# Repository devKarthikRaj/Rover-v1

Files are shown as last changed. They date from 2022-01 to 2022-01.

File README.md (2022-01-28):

# Rover-v1
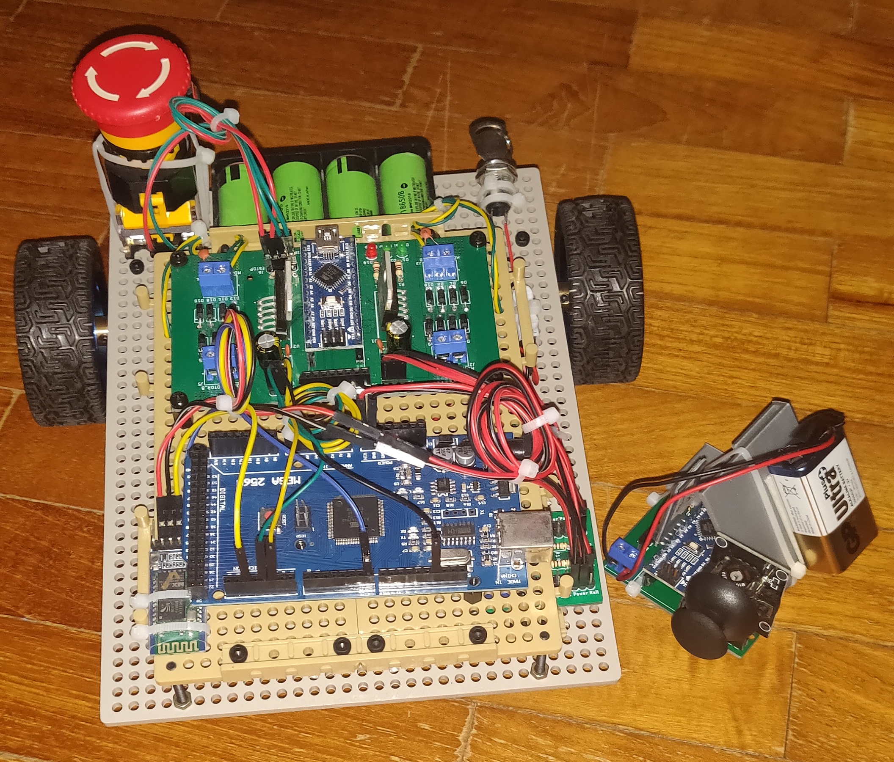
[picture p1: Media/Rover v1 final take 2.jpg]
Rover v1 final take 2
<br>
<b>Rover v1 Documentation <br> 
Initial build completed on 21st January 2022.<br>
The inital build is a joystick controlled rover. <br>
Created for my own reference in the future and for any interested engineer wannabes (like myself) out there! <br> </b>

## Quick Reference
<b>Electrical</b> <br>
<i>Eagle PCBs</i> <br>
[Power Distribution Board](https://github.com/devKarthikRaj/Rover-v1/tree/master/Electrical/PCBs/Power%20Distribution%20Board/PDB%20v0) <br>
[Motor Driver](https://github.com/devKarthikRaj/Rover-v1/tree/master/Electrical/PCBs/Not%20in%20Use/Motor%20Driver/Rover%20MDrv%20v1) <br>
[Motor Controller](https://github.com/devKarthikRaj/Rover-v1/tree/master/Electrical/PCBs/Motor%20Controller/MCon%20v1) <br>
[Remote Control](https://github.com/devKarthikRaj/Rover-v1/tree/master/Electrical/PCBs/Remote%20Control/Rover%20Bt%20Remote) <br>

<i>Arduino Header Files</i> <br>
[Rover v1 Pin Configuration Header](https://github.com/devKarthikRaj/Rover-v1/tree/master/Electrical/Firmware/Arduino%20Libraries/roverV1) <br>

<i>Arduino Firmware</i> <br>
[Low Level Controller](https://github.com/devKarthikRaj/Rover-v1/tree/master/Electrical/Firmware/Low_Level_Controller_FW) <br>
[Motor Controller](https://github.com/devKarthikRaj/Rover-v1/tree/master/Electrical/Firmware/Motor_Controller_FW) <br>
[Remote Control](https://github.com/devKarthikRaj/Rover-v1/tree/master/Electrical/Firmware/Remote_Control_FW) <br>

<i>Overall Electrical System</i> <br>
[Block Diagram](https://github.com/devKarthikRaj/Rover-v1/blob/master/Electrical/Overall%20Electrical%20System/Overall%20Block%20Diagram/Overall%20Block%20Diagram.png) <br>
[Eagle Schematic](https://github.com/devKarthikRaj/Rover-v1/blob/master/Electrical/Overall%20Electrical%20System/Overall%20Schematic/Rover%20Overalls/Rover%20v1%20Overall.sch) <br>

<b>Mechanical</b> <br>
[Motor Mount Fusion 360 File](https://github.com/devKarthikRaj/Rover-v1/blob/master/Mechanical/Not%20in%20Use/Motor%20Mount%20v1.f3d) <br>
[Motor Mount GrabCAD](https://grabcad.com/library/gearbox-dc-motor-mount-1)<br>

___

# How it all came together
Warning - This is a long read! <br>

## I had been wanting to build something like this for quite a while now.  
I thought this would be easy and wouldn't take that long. Boy, was I wrong! Nevertheless, I had loads of fun doing this. Especially when everything worked! <br>

## A rocky start...
Kicked off the project by designing the mechanical aspect of the rover in Fusion 360 CAD. Initially decided to use those low cost yellow DC gear motors. YEAH I KNOW RIGHT, these motors are a pain to use just because they don't come with a mount, its not easy to mount these motors to ANYTHING! <br><br>
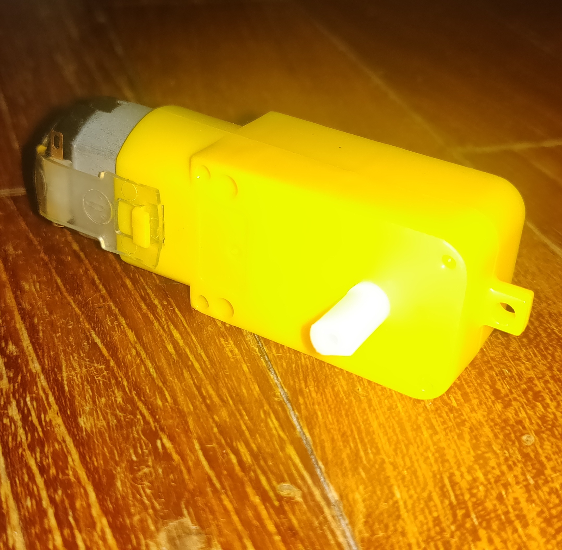
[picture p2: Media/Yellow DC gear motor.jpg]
Yellow DC gear motor
 <br>

So, I went on to CAD out a mount for these motors. <br>
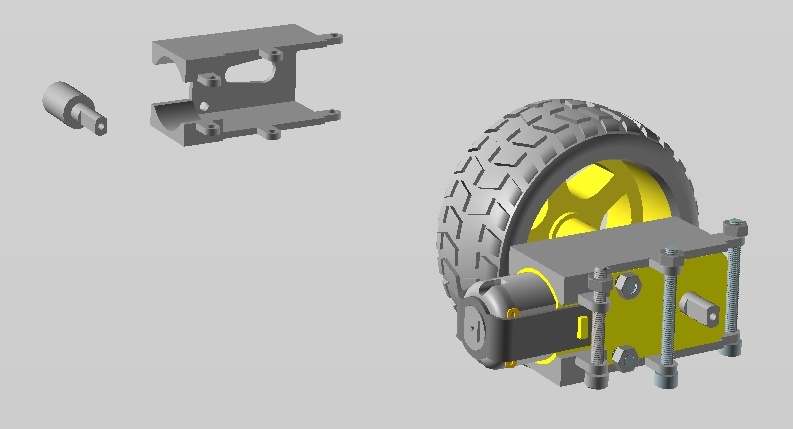
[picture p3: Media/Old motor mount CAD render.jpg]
Old motor mount CAD render
 <br>

Eventually, I got the motor mounts 3D printed and assembled them. Functionality wise, these mounts were pretty good. Structurally, the screw holders at the side were too thin and broke off if stressed too much; but hey, the mounts got the job done... I'll let that pass! <br>
<div align="center">
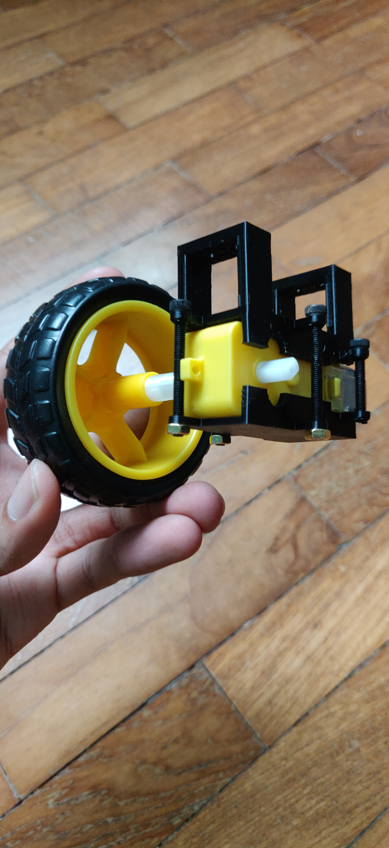
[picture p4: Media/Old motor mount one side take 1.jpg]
Old motor mount one side take 1
     
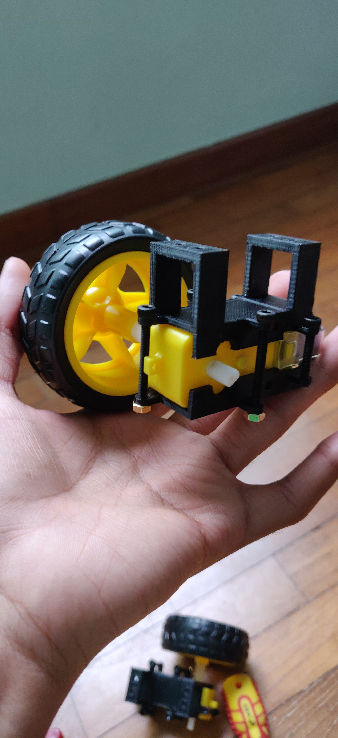
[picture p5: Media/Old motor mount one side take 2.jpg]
Old motor mount one side take 2
    
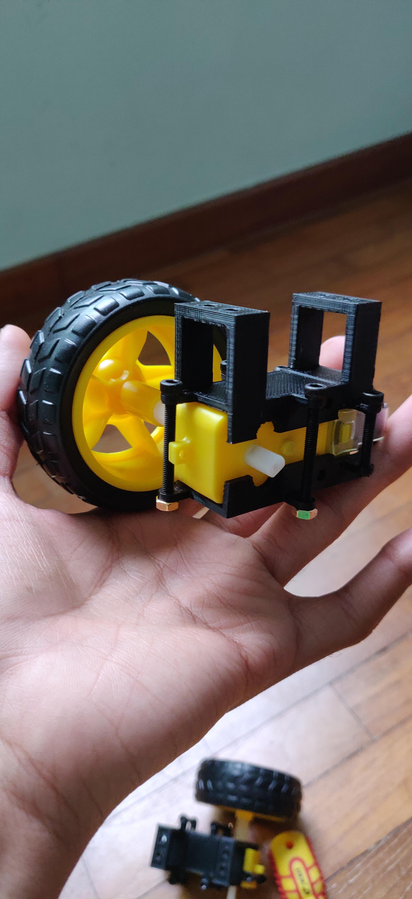
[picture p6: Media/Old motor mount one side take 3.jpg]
Old motor mount one side take 3
    
</div> <br>
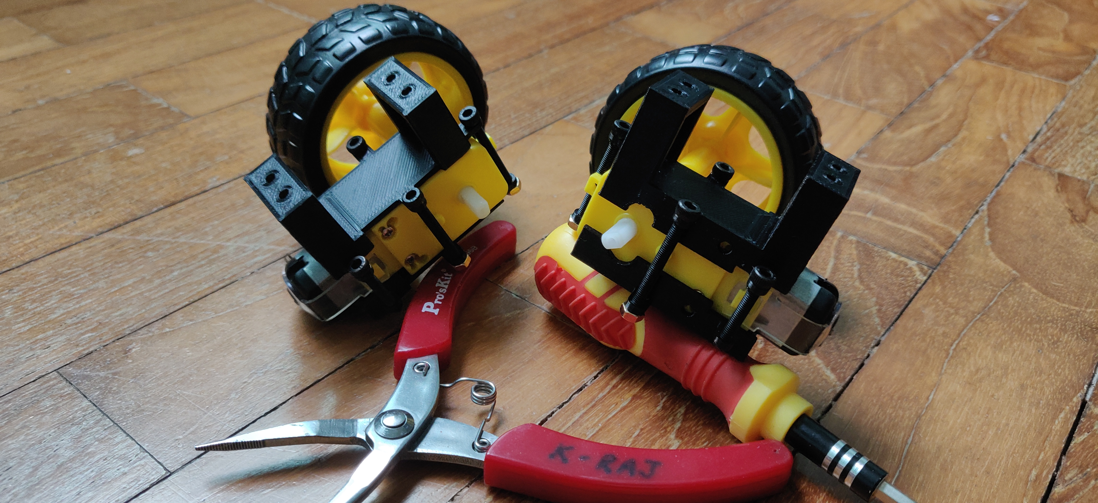
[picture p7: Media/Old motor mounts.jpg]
Old motor motor mounts
 <br>  
You can find these mounts on <a href="https://grabcad.com/library/gearbox-dc-motor-mount-1">GrabCAD</a> if you need the files. Feel free to use it. Give it a like too, that'll make my day! <br>

Motor mounts done. Need to mount them to something right? Its time to design the robot base. Came up with a race car/skateboard like shape for the base. <br>
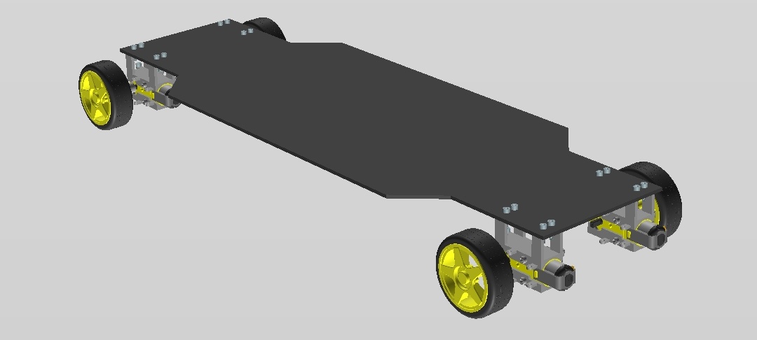
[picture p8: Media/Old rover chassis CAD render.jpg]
Old rover chassis CAD render
 <br>

I laser cut the base and attached the motor mounts with the motor to the base. The chassis looked real good. <br> 
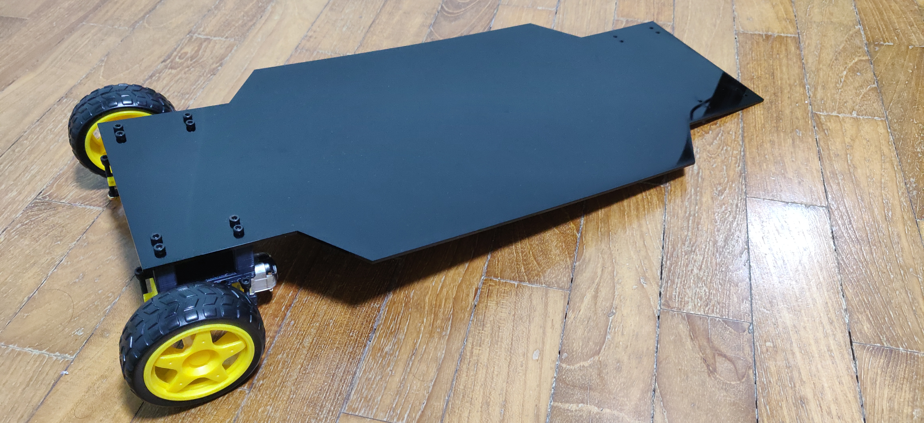
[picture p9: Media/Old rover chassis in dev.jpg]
Old rover chassis in dev
 <br>

I managed to complete only half the chassis though. Around this time, I graduated from school and lost access to all those wonderful machines (laser cutters, 3D printers, drills and stuff). Gone with the wind! There are 3D printing shops out there that offer low cost small scale printing for hobbyists like me! The problem was with finding a laser cutting shop or even a CNC shop for that matter - every place was expensive and only accepted large scale orders. Not hobbyist friendly. With a heavy heart... I discarded my beautiful half cooked chassis and took a break from the mechanical aspect. <br>

## A fresh start...
I started on the electrical aspect instead. My goal was to finish the electrical aspect first and then design the mechanical aspect accordingly to fit all the PCBs. Started out with the power circuit. 18650 Li-Ion batteries were my go to choice. Why? Surprisingly, 18650 Li-Ion batteries turned out to be cheaper than Li-Po batteries. Plus, Li-Ion is better than Li-Po as it has a higher power density... More juice in a smaller form factor! Next, I knew I'd need to step down the battery voltage to two different voltages. 5V for the digital circuitry and 6V to 12V for the motors. This is where the project kind of stagnated for a while. I really wanted to design a SMD PCB for the power circuit. THT PMICs were outdated and dissipated too much power which essentially means that the chip gets really HOT. Hot ain't good. SMD it is! THT is a no go! I designed 3 to 4 SMD power PCBs and got them manufactured. Next came the soldering, this is were I ran into a wall. Struggled with SMD soldering. Especially the IC chips. Those things are evil. This took too much of my time. Flushed that down the drain as well! Did some cheating here, I decided to buy pre-made power regulator boards. One for each voltage I required. They worked flawlessly! I'll definitely return to SMD and SMD soldering soon, maybe with a reflow hot plate, but not for this project! <br>

Next comes the motor circuitry. Started by designing a motor driver using the L298N H-bridge motor driver IC chip. It worked on the first try! I got lucky I guess! I wanted to step things up a notch. So, I went on to design a motor controller PCB. Basically, a motor driver circuit accompanied by a microcontroller (MCU). The MCU enables other PCBs to communicate with the motor controller through SPI. The MCU basically makes the motor controller "smart". It now has a brain. 
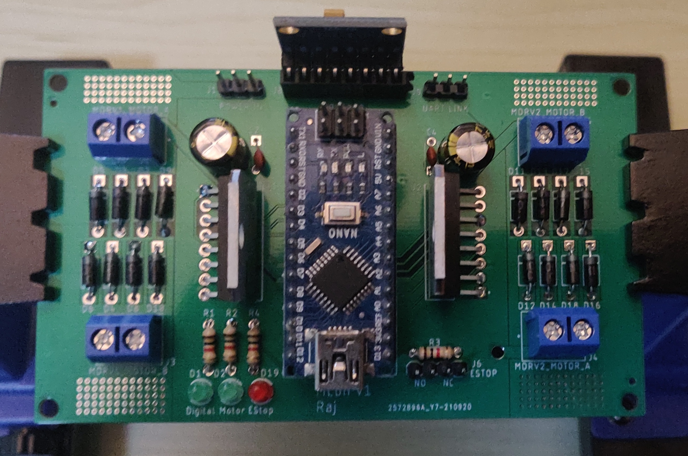
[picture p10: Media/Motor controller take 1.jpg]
Motor controller
 <br><br> 

The motor controller can be hooked up with an emergency stop (eStop) switch too.
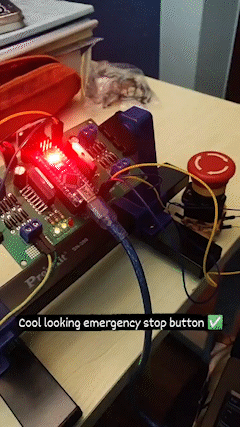
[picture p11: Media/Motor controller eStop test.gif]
Motor controller eStop test
 <br> 
 
Motor controller in action:
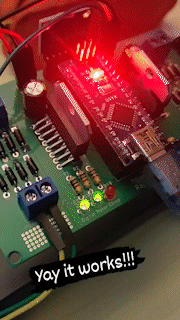
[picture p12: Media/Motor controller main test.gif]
Motor controller in action
 <br>

### An emotional rollercoaster...
Sad story incoming. On top of all that, I also added a provision for an accelerometer module to be interfaced with the MCU on the motor controller board. The whole point of the accelerometer was to make the robot go straight. Supplying the exact same voltage to two motors of the same model will not make them spin at exactly the same rate. One motor "might" be slightly faster than the other. Every motor is different. The robot won't move in a straight line unless I have feedback control to ensure that the robot moves in a straight line. Instead of using a motor fitted with an encoder to measure distance travelled by each wheel and then feedback to the MCU to adjust accordingly, I thought of trying something new. Using an accelerometer module to measure the distance. This turned out to be extremely challenging. To obtain distance from an accelerometer, you'd have to double integrate and the result is extremely inaccurate. Espcially over time, the error increases exponentially. The accelerometer did work though. For the record, I managed to get data out of the accelerometer:
<div align="center">Accelerometer in action</div> <br> 
Since that was a dead end, I dropped the accelerometer and tried using a compass magnetometer module to measure heading. Then, orientate the robot accordingly if the robot is off course. Long story short, this turned out to be difficult as well. The compass outputs x,y,z axis values. With this I know which direction the robot is facing. However, translating this data into PWM commands to supply to the motor controller to adjust the heading of the robot proved to be challenging. I wanted to use PID control for this but I couldn't establish a link between the INPUT (magnetometer's x,y,z values) and the OUTPUT (PWM motor values). Ended up scrapping that idea as well. *Cry cry* <br> 
Pro tip - Best way to measure distance travelled by a robot is to use motors with encoders! I think I've learnt a very good lesson here :) <br> <br>

The only PCB left to work on was the PCB to distribute the two voltages to their own power rails so that the other PCBs can tap from these rails. Very simple. No complex circuits involved. This didn't take too long to get done.

## So done with the mechanical aspect...
Since I lost access to all those machines in school post graduation, I decided to get Tamiya parts. Tamiya has a lot of versatile products and its low cost, just what I was looking for. I also decided to use stronger motors. From a previous partially working obstacle sensor robot project, I knew that those yellow gear motors can't carry heavy loads. This robot was leaning on the heavier side. Especially with four 18650 batteries. So I bought some machifit gear motors, slightly more expensive than the yellow gear motors, but these machifit motors come with their own mount and nuts & bolts and can be hooked up to almost anything! How nice!  

Since the motor controller was an "overall" success and since I secured all the Tamiya mechanical parts from Japan and new motors from China, It was time to hook everything up. 
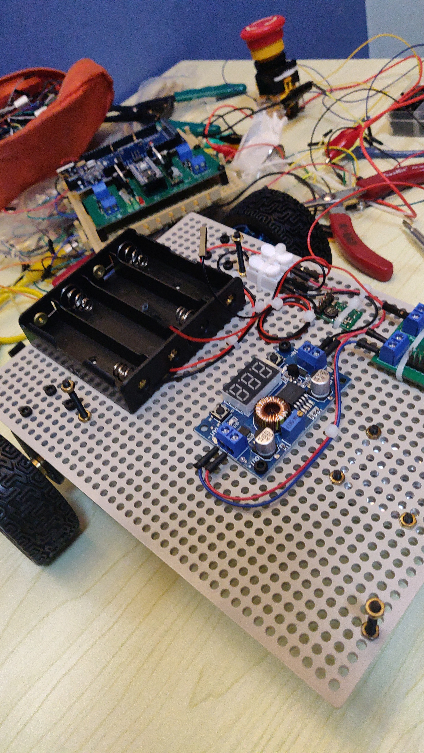
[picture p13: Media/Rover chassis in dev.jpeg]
Rover chassis in dev
 <br>

## A hot mess...
Yes. I know the whole rover sounds like a hot mess (not literally... my PCBs are cool as cucumbers). So, here's the block diagram of the rover's electrical system. The big picture:
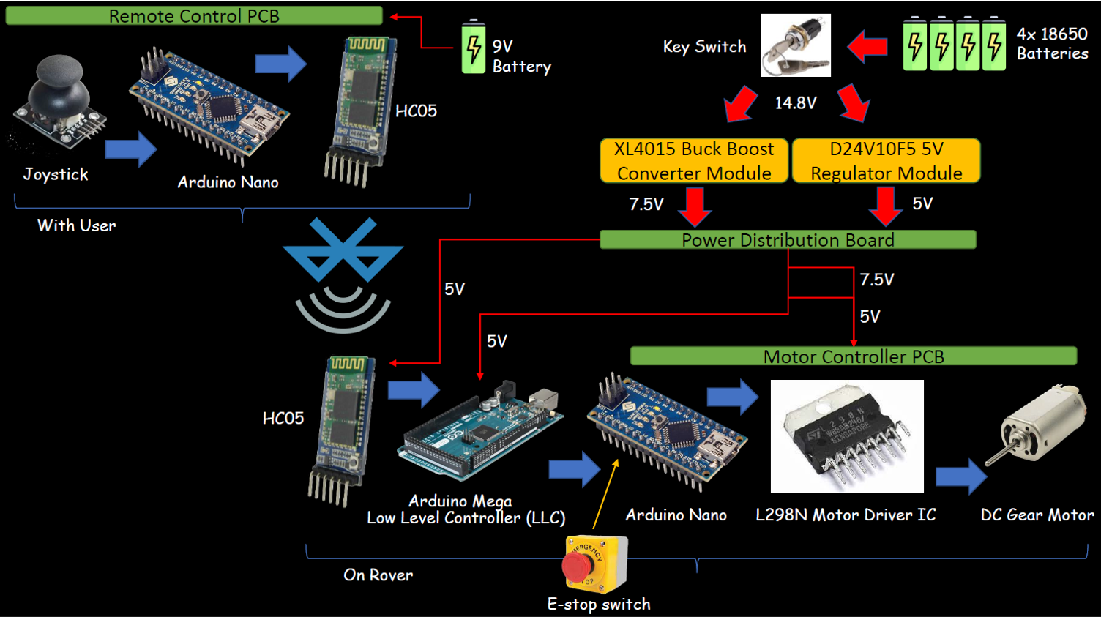
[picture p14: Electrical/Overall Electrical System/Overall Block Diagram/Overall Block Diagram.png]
Overall Electrical System Block Diagram

The so called "low level controller (LLC)" here acts as a middle man. The low level controller is just an Arduino Mega board. The LLC communicates with the remote control for the rover via Bluetooth and sends the data received from the Bluetooth remote to the motor controller via SPI. In the future, if I add sensors to this rover, the sensors will also interact with the low level controller. The low level controller will process the sensor data and send control signals to the motor controller accordingly. Having the LLC will hopefully allow me to upgrade this rover hassle free in the future!   

The assembly was smooth as butter. The entire electrical system was wired up and "WORKING" on my table. That's what I'm talking about! Robot on table:
<div align="center">Robot on table</div> <br> 

Last but not least - the firmware for all the MCUs on the rover and the Bluetooth remote. Writing firmware is always fun. Even though I encountered half a million exceptions. I'm kidding. 
## Baby steps
The first time the rover moved...
<div align="center">baby steps</div> <br> 

## Rover gone mad
Bug filled code creating chaos...
<i>This was when I was still trying to control the robot using the accelerometer and magnetometer</i>
<div align="center">Rover gone mad</div> <br> 

## Rover in action!
It works!
<div align="center">Rover in action</div> <br>

Oh oh... I totally forgot about the remote control. It was still contained on a breadboard, running off my old Arduino Uno. Quickly made a THT PCB and got it manufactured and soldered. Took about a few hours to design the PCB in Eagle and 2 weeks for it to be delivered. Soldered it and boom! Done! One good thing that came about from designing so many failed PCBs - now I can whip up simple "WORKING" boards in a few hours... Yay!
<div align="center">
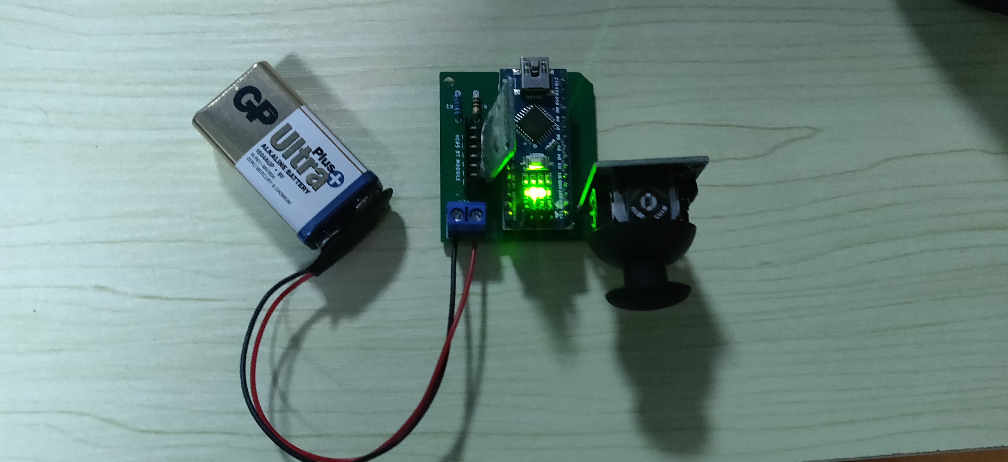
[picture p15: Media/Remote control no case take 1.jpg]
Remote control no case take 1
    
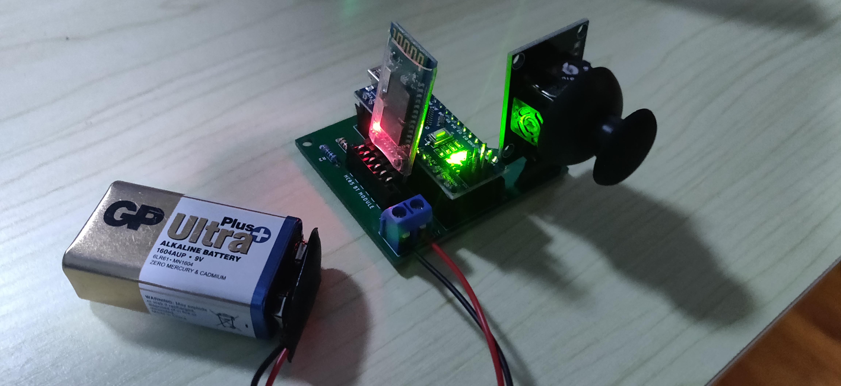
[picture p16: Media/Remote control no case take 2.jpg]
Remote control no case take 2
    
</div>
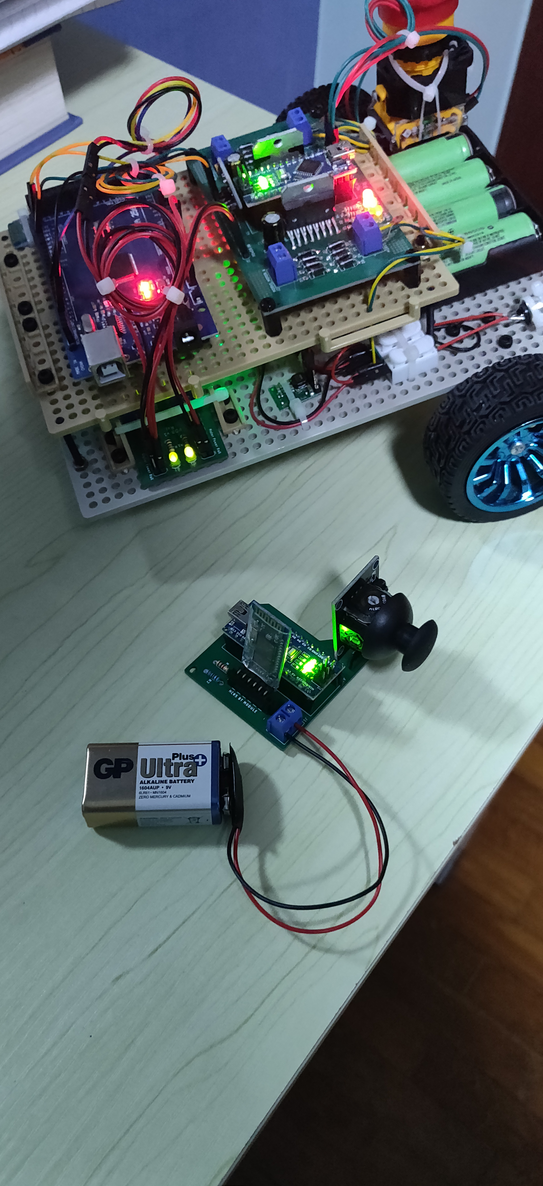
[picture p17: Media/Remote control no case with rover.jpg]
Remote control no case with rover
 <br>

The remote control needed a case! Luckily I saved some unused 3D printed acrylic mounts from a school project a few years ago. Zip tied the remote control PCB and stuck the 9V battery to the mount.
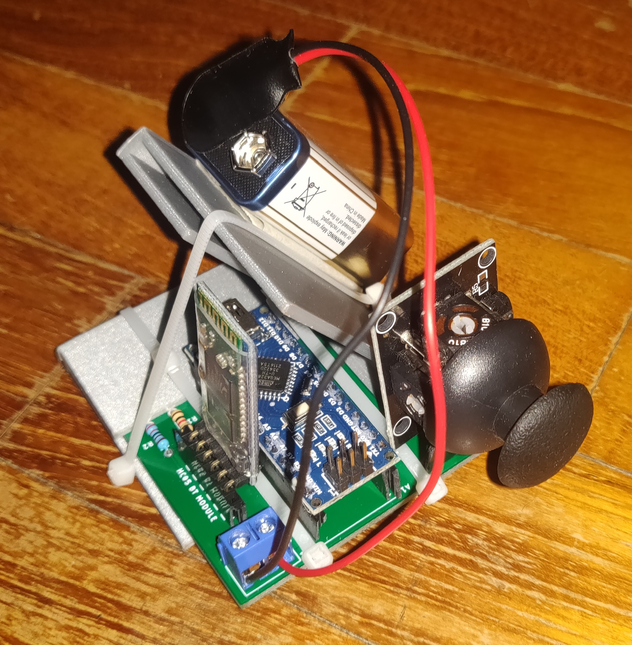
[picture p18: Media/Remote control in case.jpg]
Remote control in case
 <br>

Stick a fork in it people! We done!
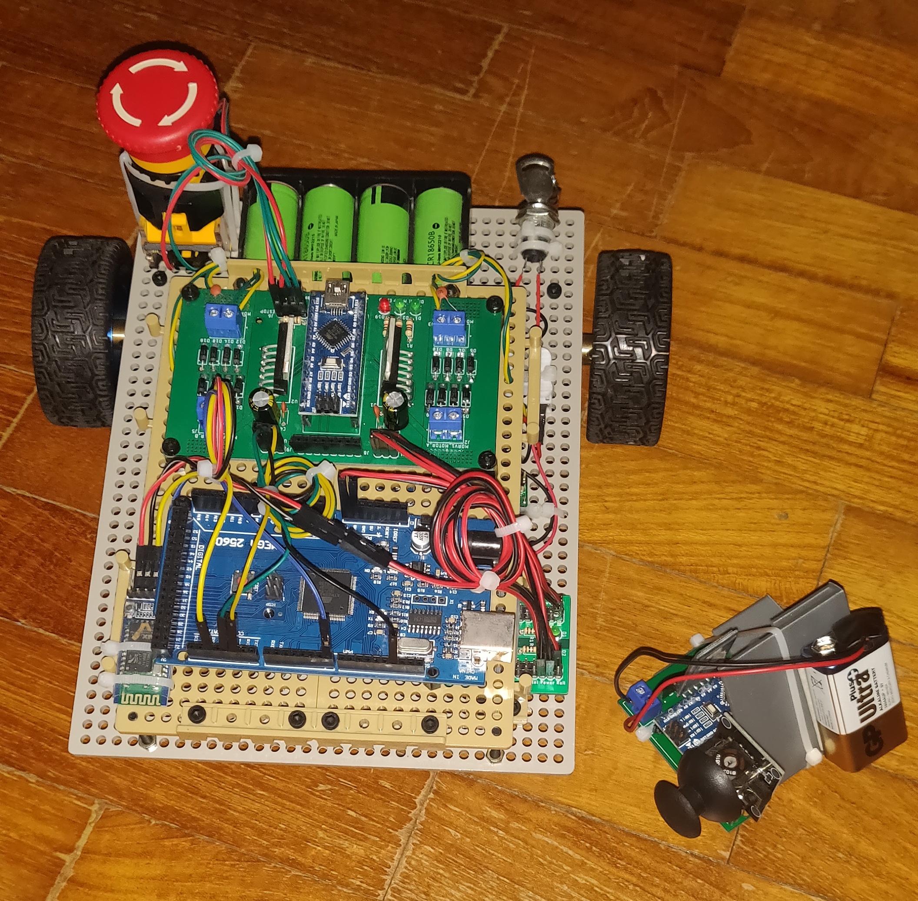
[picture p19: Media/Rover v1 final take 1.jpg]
Rover v1 final take 1


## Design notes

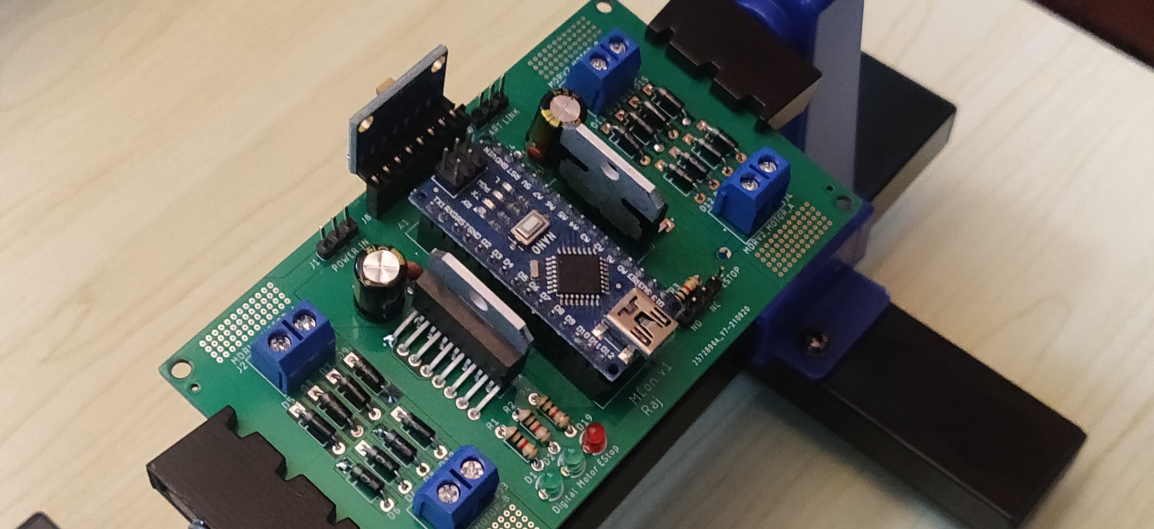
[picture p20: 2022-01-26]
Media/Motor Controller take 2.jpg

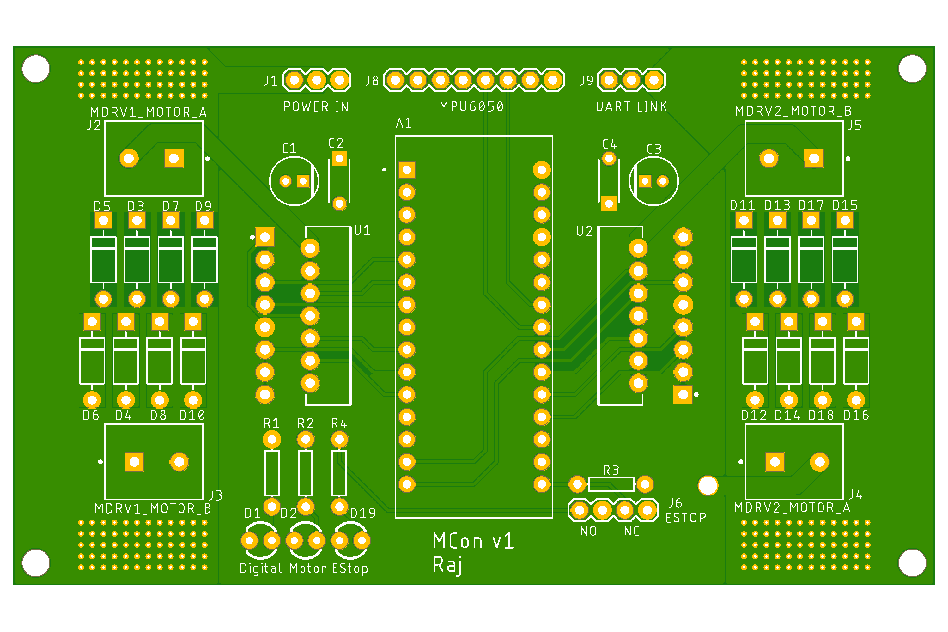
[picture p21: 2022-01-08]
Electrical/PCBs/Motor Controller/MCon v1/MCon_v1_Top.png

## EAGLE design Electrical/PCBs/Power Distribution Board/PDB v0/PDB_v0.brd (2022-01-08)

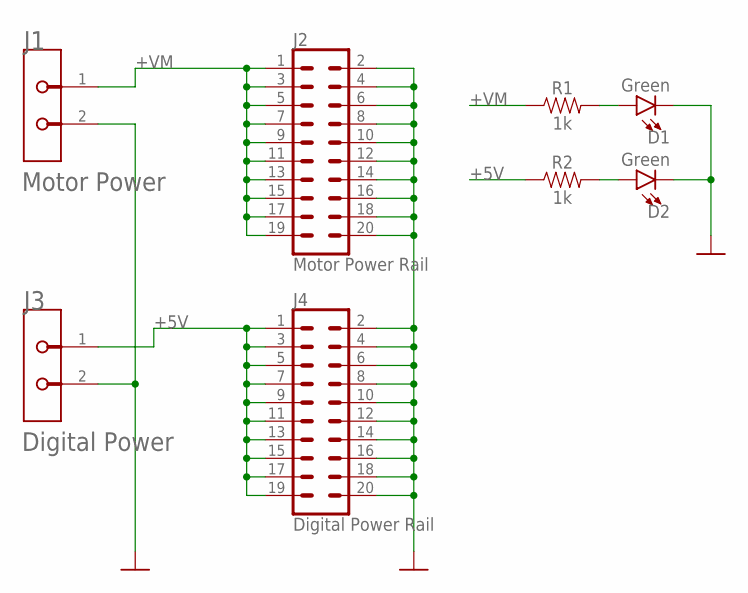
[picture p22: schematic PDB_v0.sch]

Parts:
D1, D2: Green; LED_3MM
J1: Motor Power; TE_282837-2_0
J2: Motor Power Rail; 2X10
J3: Digital Power; TE_282837-2_0
J4: Digital Power Rail; 2X10
R1, R2: 1k; AXIAL-0.3

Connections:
+5V: J3.1, J4.1, J4.3, J4.5, J4.7, J4.9, J4.11, J4.13, J4.15, J4.17, J4.19, R2.P$1 (1)
+VM: J1.1, J2.1, J2.3, J2.5, J2.7, J2.9, J2.11, J2.13, J2.15, J2.17, J2.19, R1.P$1 (1)
GND: D1.K (C), D2.K (C), J1.2, J2.2, J2.4, J2.6, J2.8, J2.10, J2.12, J2.14, J2.16, J2.18, J2.20, J3.2, J4.2, J4.4, J4.6, J4.8, J4.10, J4.12, J4.14, J4.16, J4.18, J4.20
unnamed: D1.A, R1.P$2 (2)
unnamed: D2.A, R2.P$2 (2)

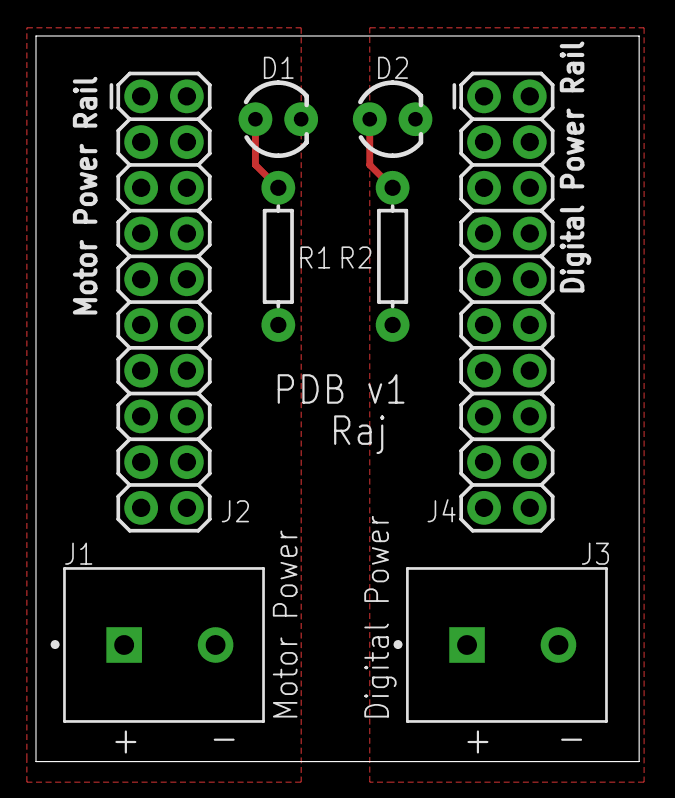
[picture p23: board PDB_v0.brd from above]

Board: 2 copper layers, 33.5 x 40.3 mm, 8 parts (0 on the bottom side), 5 nets.

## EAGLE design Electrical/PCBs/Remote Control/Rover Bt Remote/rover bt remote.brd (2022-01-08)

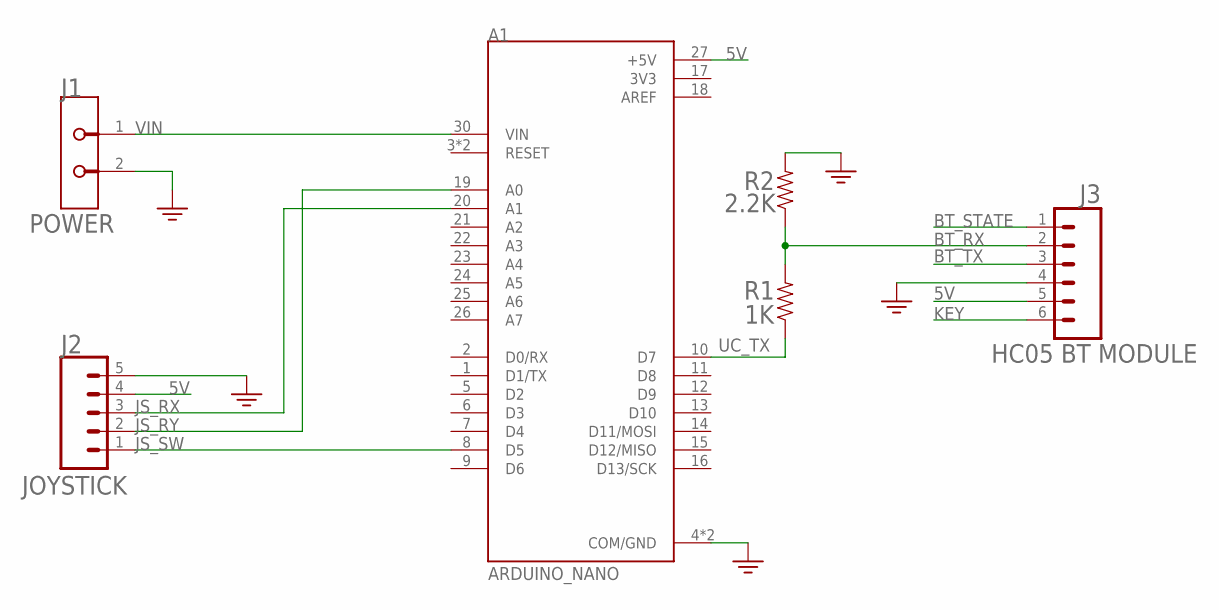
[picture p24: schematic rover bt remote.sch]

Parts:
A1: ARDUINO_NANO; SHIELD_ARDUINO_NANO
J1: POWER; TE_282837-2_0
J2: JOYSTICK; 1X05
J3: HC05 BT MODULE; 1X06
R1: 1K; AXIAL-0.3
R2: 2.2K; AXIAL-0.3

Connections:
3V3: A1.17 (3V3)
5V: A1.27 (+5V), J2.4, J3.5
AREF: A1.18 (AREF)
BT_RX: J3.2, R1.P$2 (2), R2.P$1 (1)
BT_STATE: J3.1
BT_TX: J3.3
GND: A1.4 (COM/GND), A1.29 (COM/GND), J1.2, J2.5, J3.4, R2.P$2 (2)
JS_RX: A1.20 (A1), J2.3
JS_RY: A1.19 (A0), J2.2
JS_SW: A1.8 (D5), J2.1
KEY: J3.6
UC_TX: A1.10 (D7), R1.P$1 (1)
VIN: A1.30 (VIN), J1.1

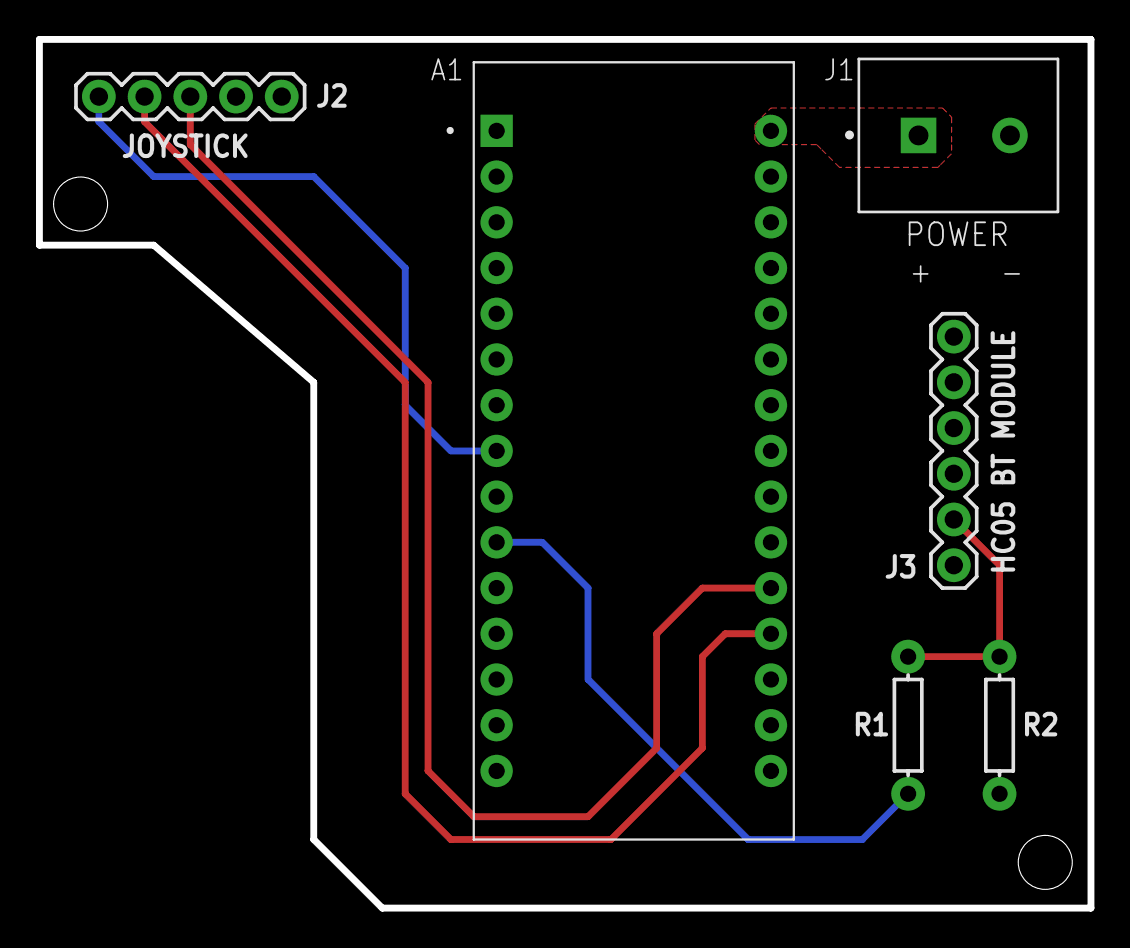
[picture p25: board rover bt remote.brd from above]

Board: 2 copper layers, 58.4 x 48.3 mm, 6 parts (0 on the bottom side), 8 nets.

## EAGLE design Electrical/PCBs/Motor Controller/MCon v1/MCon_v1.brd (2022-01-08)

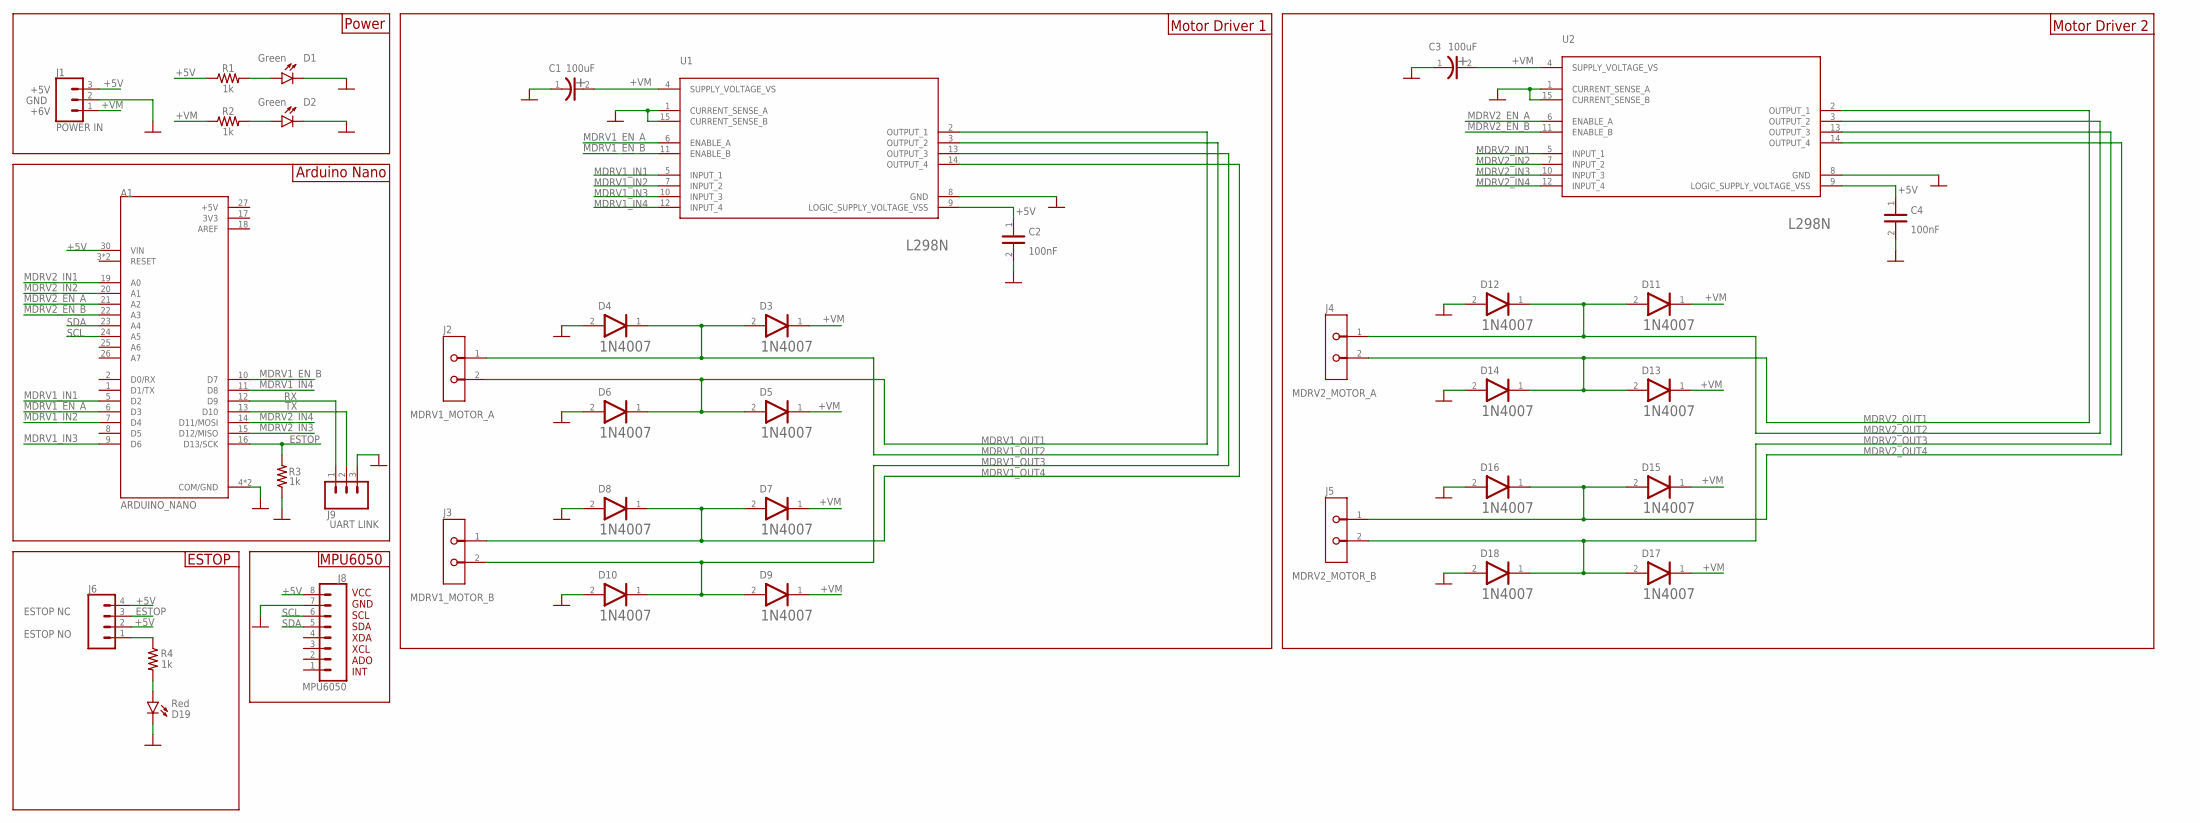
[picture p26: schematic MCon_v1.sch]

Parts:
A1: ARDUINO_NANO; SHIELD_ARDUINO_NANO
C1, C3: 100uF; PANASONIC_EEU-FR1C101_0
C2, C4: 100nF; AVX_CK05BX104K_0
D1, D2: Green; LED_3MM
D3, D4, D5, D6, D7, D8, D9, D10, D11, D12, D13, D14, D15, D16, D17, D18: DIOTEC_1N4007DIOTEC_1N4007_0_0; DIOTEC_1N4007_0
D19: Red; LED_3MM
J1: POWER IN; 1X03
J2: MDRV1_MOTOR_A; TE_282837-2_0
J3: MDRV1_MOTOR_B; TE_282837-2_0
J4: MDRV2_MOTOR_A; TE_282837-2_0
J5: MDRV2_MOTOR_B; TE_282837-2_0
J6: CONN_04PTH; 1X04
J8: MPU6050; 1X08
J9: UART LINK; 1X03
R1, R2, R3, R4: 1k; AXIAL-0.3
U1, U2: STMICROELECTRONICS_L298NSTMICROELECTRONICS_L298N_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; STMICROELECTRONICS_L298N_0

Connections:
3V3: A1.17 (3V3)
+5V: A1.27 (+5V), A1.30 (VIN), C2.1, C4.1, J1.3, J6.2, J6.4, J8.8, R1.P$1 (1), U1.9 (LOGIC_SUPPLY_VOLTAGE_VSS), U2.9 (LOGIC_SUPPLY_VOLTAGE_VSS)
+VM: C1.2 (ANODE), C3.2 (ANODE), D3.1 (CATHODE), D5.1 (CATHODE), D7.1 (CATHODE), D9.1 (CATHODE), D11.1 (CATHODE), D13.1 (CATHODE), D15.1 (CATHODE), D17.1 (CATHODE), J1.1, R2.P$1 (1), U1.4 (SUPPLY_VOLTAGE_VS), U2.4 (SUPPLY_VOLTAGE_VS)
AREF: A1.18 (AREF)
ESTOP: A1.16 (D13/SCK), J6.3, R3.P$2 (2)
GND: A1.4 (COM/GND), A1.29 (COM/GND), C1.1 (CATHODE), C2.2, C3.1 (CATHODE), C4.2, D1.K (C), D2.K (C), D4.2 (ANODE), D6.2 (ANODE), D8.2 (ANODE), D10.2 (ANODE), D12.2 (ANODE), D14.2 (ANODE), D16.2 (ANODE), D18.2 (ANODE), D19.K (C), J1.2, J8.7, J9.3, R3.P$1 (1), U1.1 (CURRENT_SENSE_A), U1.8 (GND), U1.15 (CURRENT_SENSE_B), U2.1 (CURRENT_SENSE_A), U2.8 (GND), U2.15 (CURRENT_SENSE_B)
MDRV1_EN_A: A1.6 (D3), U1.6 (ENABLE_A)
MDRV1_EN_B: A1.10 (D7), U1.11 (ENABLE_B)
MDRV1_IN1: A1.5 (D2), U1.5 (INPUT_1)
MDRV1_IN2: A1.7 (D4), U1.7 (INPUT_2)
MDRV1_IN3: A1.9 (D6), U1.10 (INPUT_3)
MDRV1_IN4: A1.11 (D8), U1.12 (INPUT_4)
MDRV1_OUT1: D5.2 (ANODE), D6.1 (CATHODE), J2.2, U1.2 (OUTPUT_1)
MDRV1_OUT2: D3.2 (ANODE), D4.1 (CATHODE), J2.1, U1.3 (OUTPUT_2)
MDRV1_OUT3: D9.2 (ANODE), D10.1 (CATHODE), J3.2, U1.13 (OUTPUT_3)
MDRV1_OUT4: D7.2 (ANODE), D8.1 (CATHODE), J3.1, U1.14 (OUTPUT_4)
MDRV2_EN_A: A1.21 (A2), U2.6 (ENABLE_A)
MDRV2_EN_B: A1.22 (A3), U2.11 (ENABLE_B)
MDRV2_IN1: A1.19 (A0), U2.5 (INPUT_1)
MDRV2_IN2: A1.20 (A1), U2.7 (INPUT_2)
MDRV2_IN3: A1.15 (D12/MISO), U2.10 (INPUT_3)
MDRV2_IN4: A1.14 (D11/MOSI), U2.12 (INPUT_4)
MDRV2_OUT1: D13.2 (ANODE), D14.1 (CATHODE), J4.2, U2.2 (OUTPUT_1)
MDRV2_OUT2: D11.2 (ANODE), D12.1 (CATHODE), J4.1, U2.3 (OUTPUT_2)
MDRV2_OUT3: D17.2 (ANODE), D18.1 (CATHODE), J5.2, U2.13 (OUTPUT_3)
MDRV2_OUT4: D15.2 (ANODE), D16.1 (CATHODE), J5.1, U2.14 (OUTPUT_4)
unnamed: D1.A, R1.P$2 (2)
unnamed: D2.A, R2.P$2 (2)
unnamed: J6.1, R4.P$1 (1)
unnamed: D19.A, R4.P$2 (2)
RX: A1.12 (D9), J9.1
SCL: A1.24 (A5), J8.6
SDA: A1.23 (A4), J8.5
TX: A1.13 (D10), J9.2

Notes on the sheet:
+5V
GND
+6V
Power
Motor Driver 1
Motor Driver 2
ESTOP
VCC GND SCL SDA XDA XCL ADO INT
MPU6050
Arduino Nano
ESTOP NC ESTOP NO

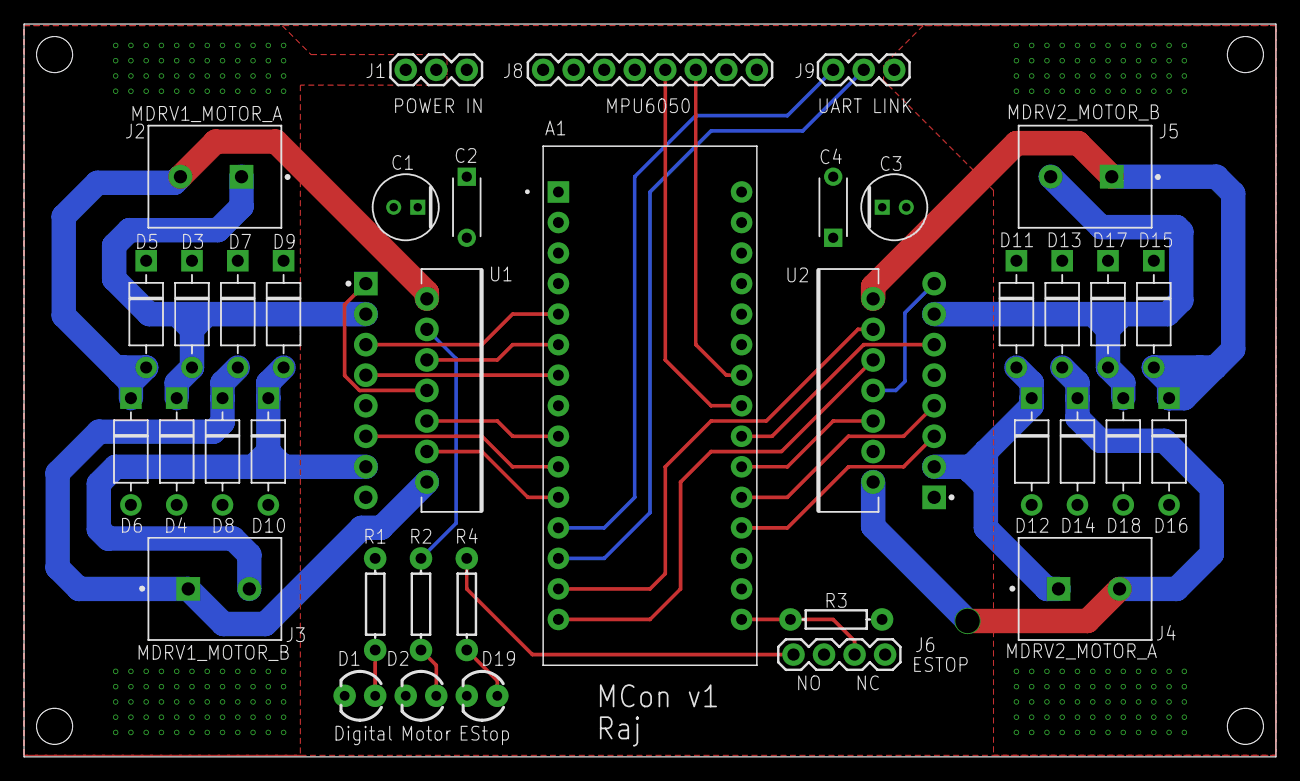
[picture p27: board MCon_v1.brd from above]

Board: 2 copper layers, 104.1 x 61.0 mm, 38 parts (0 on the bottom side), 32 nets.

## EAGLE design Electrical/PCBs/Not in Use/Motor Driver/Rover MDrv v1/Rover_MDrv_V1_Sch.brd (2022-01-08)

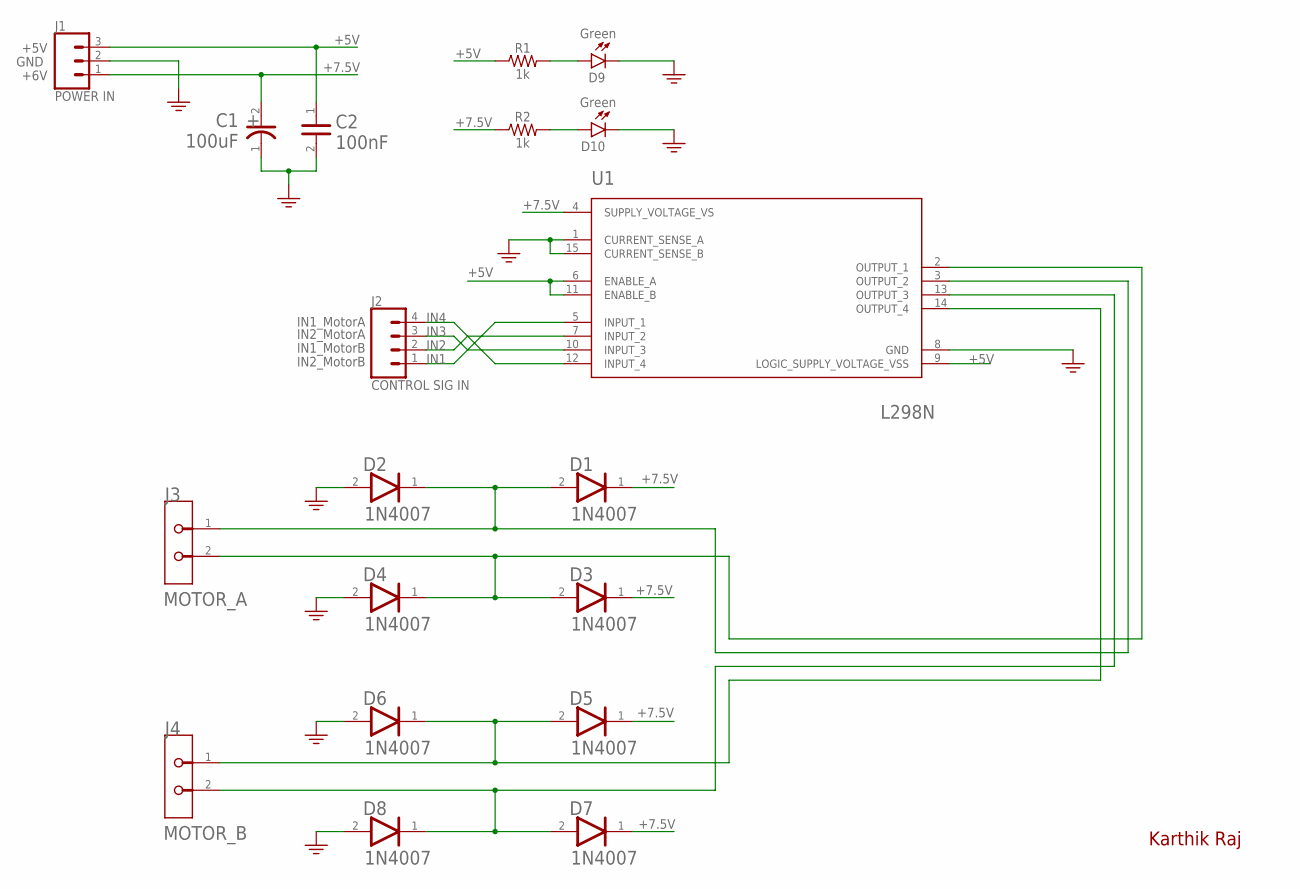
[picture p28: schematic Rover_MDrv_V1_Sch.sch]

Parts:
C1: 100uF; PANASONIC_EEU-FR1C101_0
C2: 100nF; AVX_CK05BX104K_0
D1, D2, D3, D4, D5, D6, D7, D8: DIOTEC_1N4007DIOTEC_1N4007_0_0; DIOTEC_1N4007_0
D9, D10: Green; LED_3MM
J1: POWER IN; 1X03
J2: CONTROL SIG IN; 1X04
J3: MOTOR_A; TE_282837-2_0
J4: MOTOR_B; TE_282837-2_0
R1, R2: 1k; AXIAL-0.3
U1: STMICROELECTRONICS_L298NSTMICROELECTRONICS_L298N_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; STMICROELECTRONICS_L298N_0

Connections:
+5V: C2.1, J1.3, R1.P$1 (1), U1.6 (ENABLE_A), U1.9 (LOGIC_SUPPLY_VOLTAGE_VSS), U1.11 (ENABLE_B)
+7.5V: C1.2 (ANODE), D1.1 (CATHODE), D3.1 (CATHODE), D5.1 (CATHODE), D7.1 (CATHODE), J1.1, R2.P$1 (1), U1.4 (SUPPLY_VOLTAGE_VS)
GND: C1.1 (CATHODE), C2.2, D2.2 (ANODE), D4.2 (ANODE), D6.2 (ANODE), D8.2 (ANODE), D9.K (C), D10.K (C), J1.2, U1.1 (CURRENT_SENSE_A), U1.8 (GND), U1.15 (CURRENT_SENSE_B)
IN1: J2.1, U1.5 (INPUT_1)
IN2: J2.2, U1.7 (INPUT_2)
IN3: J2.3, U1.10 (INPUT_3)
IN4: J2.4, U1.12 (INPUT_4)
unnamed: D9.A, R1.P$2 (2)
unnamed: D10.A, R2.P$2 (2)
OUT1: D3.2 (ANODE), D4.1 (CATHODE), J3.2, U1.2 (OUTPUT_1)
OUT2: D1.2 (ANODE), D2.1 (CATHODE), J3.1, U1.3 (OUTPUT_2)
OUT3: D7.2 (ANODE), D8.1 (CATHODE), J4.2, U1.13 (OUTPUT_3)
OUT4: D5.2 (ANODE), D6.1 (CATHODE), J4.1, U1.14 (OUTPUT_4)

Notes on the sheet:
+5V
GND
+6V
IN1_MotorA
IN2_MotorA
IN1_MotorB
IN2_MotorB
Karthik Raj

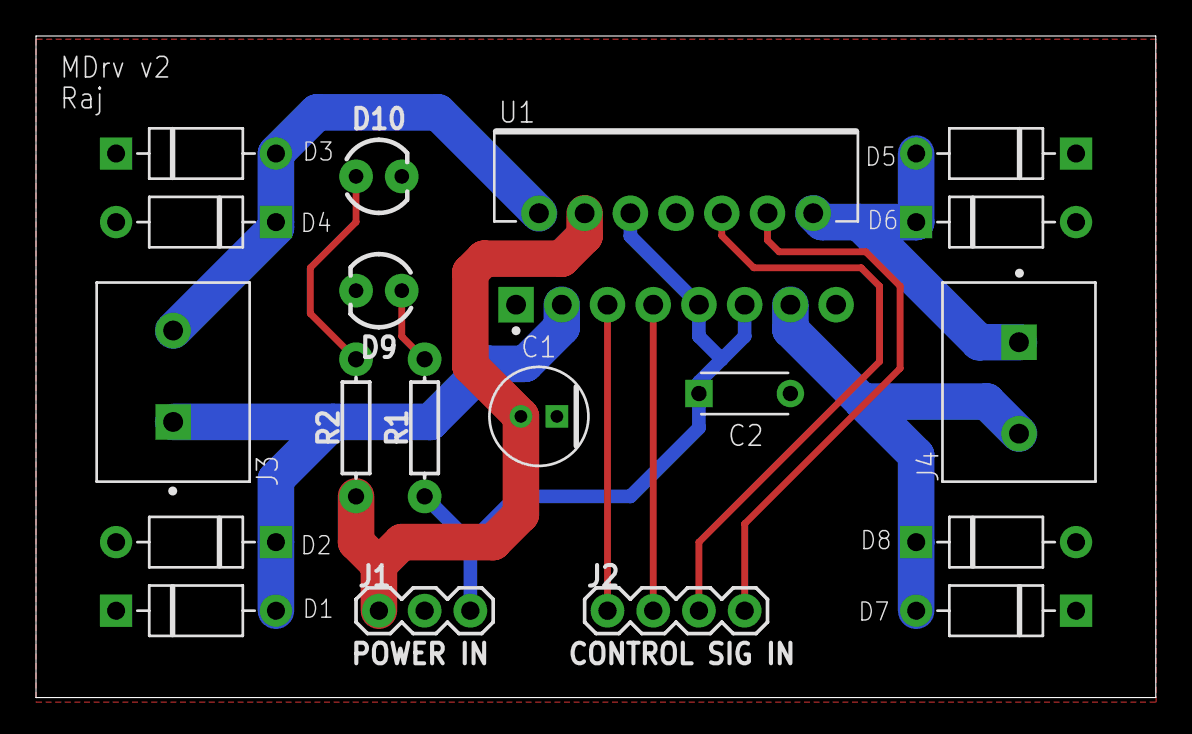
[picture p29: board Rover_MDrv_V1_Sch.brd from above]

Board: 2 copper layers, 62.2 x 36.8 mm, 19 parts (0 on the bottom side), 13 nets.

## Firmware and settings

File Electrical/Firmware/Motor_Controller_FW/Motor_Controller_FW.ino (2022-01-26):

/* Motor Controller Version 1 Firmware
 *  
 *  Code written for Arduino Nano Clone (Driver Auto Installed by Windows)
 *  
 *  UART 0 - Serial - For debugging
 *  UART 1 - uart1 - UART to low level controller
 *  
 *  This code receives and decodes joystick data and then drives the motors accordingly
 *
 *  Written By Karthik Raj 
 */

#include <SoftwareSerial.h>
#include <roverV1.h>

#define uartRx 9
#define uartTx 10

//Global Vars
int xAxisReq;
int yAxisReq;

//Define UART port for comms with LLC
SoftwareSerial uart1(uartRx, uartTx); //RX,TX
  
void setup() {
  Serial.begin(230400);
  uart1.begin(38400);

  pinMode(uartRx, INPUT);
  pinMode(uartTx, OUTPUT);
}

void loop() {
  //--- Receive and decode movement data ---
  rxMovementData(); //Updates xAxisReq andyAxisReq

  //Only for debugging
  Serial.print("Rx: ");
  Serial.print("(");
  Serial.print(xAxisReq);
  Serial.print(",");
  Serial.print(yAxisReq);
  Serial.print(")");
  Serial.print(" ");

  String motorStatus = driveMotors();
  
  //Only for debugging
  Serial.print("MotorStatus: ");
  Serial.print(motorStatus);
  Serial.print(" ");
  Serial.println();
}

/* Receive Movement Data
    If data is avaialble from LLC...
    Receive data
    Decode data
    Update reqSpeedMultiplier and reqAbsHeading
*/
void rxMovementData() {
  //if data available...
  if (uart1.available() > 0) {
    //"(" is the start byte
    if (uart1.read() == '(') {
      String _mConInString = uart1.readStringUntil(')'); //")" is the end byte
      //Serial.print(mConInString); //Only for debugging

      //Convert received mConInString to char array for further processing
      char _mConInCharArray[_mConInString.length() + 1]; //+1 to leave space for the null terminator
      _mConInString.toCharArray(_mConInCharArray, _mConInString.length() + 1);

      int _splitCharElmNum; //Element number of the '<' that splits the speed from the heading
      for (int i = 0; i < sizeof(_mConInString); i++) {
        if (_mConInString[i] == ',') {
          _splitCharElmNum = i;
        }
      }
      //Splitting the mConInCharArray into its native components - x and y
      //Decoding speed x
      char _xArray[_splitCharElmNum + 1];
      for (int i = 0; i < _splitCharElmNum; i++) {
        _xArray[i] = _mConInCharArray[i];
      }
      int _xAxis = atoi(_xArray);

      //Decoding y
      char _yArray[_splitCharElmNum + 1];
      for (int i = 0; i < (sizeof(_mConInCharArray) - 1 - _splitCharElmNum); i++) {
        _yArray[i] = _mConInCharArray[_splitCharElmNum + 1 + i];
      }
      int _yAxis = atoi(_yArray);
      
      //Pass the local vals to the global vars for use in other functions
      xAxisReq = _xAxis;
      yAxisReq = _yAxis;
    } else {
      //Serial.println("Rx'ing garbage data"); //THIS IS NOT THE RIGHT WAY TO DETECT GARBAGE DATA
    }
  }
  //if no data available...
  else {
    //Serial.println("No Data Rx'ed");
  }
}

String driveMotors() {
  String currStatus = "Init"; //Init Status
  if(digitalRead(eStop) == HIGH) {
    if(xAxisReq > 300 && xAxisReq < 800 && yAxisReq > 800) {
      //Forward-Maintain
      roverV1().moveForward();
      currStatus = "Forward-Maintain";
    } else if(xAxisReq > 300 && xAxisReq < 800 && yAxisReq < 300) {
      //Backward-Maintain
      roverV1().moveBackward();
      currStatus = "Backward-Maintain";
    } else if(xAxisReq < 300) {
      //Left
      roverV1().spinLeft();
      currStatus = "SpinLeft";
    } else if(xAxisReq > 800) {
      //Right
      roverV1().spinRight();
      currStatus = "SpinRight";
     }
  } else {
    currStatus = "Brake";
    roverV1().engageBrakes();
  }

  return currStatus;
}

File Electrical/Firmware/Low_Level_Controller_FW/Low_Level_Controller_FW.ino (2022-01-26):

/* Rover Version 1 Mark I Low Level Controller Firmware
 *  
 *  Receive encoded movement data from master over Bluetooth link.
 *  Send encoded movement data to motor controller over UART link.
 *  
 *  Code written for Arduino Mega Clone (Driver Auto Installed by Windows)
 *  
 *  UART 0 - Serial - For debugging
 *  UART 1 - Serial1 - Bluetooth link (wireless UART)
 *  UART 2 - Serial2 - UART to motor controller
 *  
 *  The low level controller acts as a middleman between the remote and the motor controller
 *  This code receives joystick data over Bluetooth and sends it to motor controller over UART
 *  
 *  Written By Karthik Raj
 */

#define hc05_state 7

void setup() {
  Serial.begin(38400);
  Serial1.begin(38400); //HC05 chips are configured to exchange data at 38400 baud
  Serial2.begin(38400);

  pinMode(hc05_state, INPUT);
}

void loop() {
  //stuff
  if(digitalRead(hc05_state) == HIGH) {
    //If data available...
    if(Serial1.available()>0) {
      char i = Serial1.read(); //Read the movement data from master over the Bluetooth link and store it in a char
      Serial2.print(i); //Send the stored movement data to the motor controller over UART
      Serial.print(i); //For debugging only
    }
    //if no data available... 
    else {
      //Serial.println("No data received from master"); //Only for debugging
    }
  } else {
    Serial2.print("(512,512)");
    Serial.println("BT Connection Lost"); //For debugging only
  }
}

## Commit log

2022-01-09 Added in overalls and firmware header comments
    [Rover v1 Overall.sch]
2022-01-26 Bug fixes and added pictures
    [Low_Level_Controller_FW.ino, Motor_Controller_FW.ino, Remote_Control_FW.ino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]

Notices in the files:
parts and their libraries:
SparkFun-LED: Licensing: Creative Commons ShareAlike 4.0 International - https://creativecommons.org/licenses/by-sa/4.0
